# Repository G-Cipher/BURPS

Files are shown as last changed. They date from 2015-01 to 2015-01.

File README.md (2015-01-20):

BURPS
=====

BeagleBone Universal Removed Pololu Steppers

BeagleBone Black cape providing a semi-generic optoisolated breakout for 4
stepper axis outputs and 3 limit switch inputs. The BBB I/O pin configuration
is chosen for compatibility with [BeagleG] for testing purposes.
Output is a male DB-25 connector, with pinout selected for compatibility with
[FlashCut CNC] stepper driver electronics.

BURPS is therefore a stripped-down implementation of [BUMPS], the
BeagleBone Universal Multi Pololu Steppers board.

The BURPS PCB design files were created with [Cadsoft Eagle] 5.12.0. This
board is designed for a prototype milling process, and may not be suitable
for commercial fabrication.

PCB v1.0 uses a male DB-25 connector mounted on the bottom of the board for
external signals. This was found to conflict with peripherals plugged into
the USB type A or micro HDMI ports.

PCB v1.1 replaces the DB-25 connector with a dual-row 26-pin header. The
pinout of the header corresponds to a male DB-25. A ribbon cable assembly
with header IDC and male DB-25 IDC will connect the signals correctly.

The graphics below depict PCB v1.0.

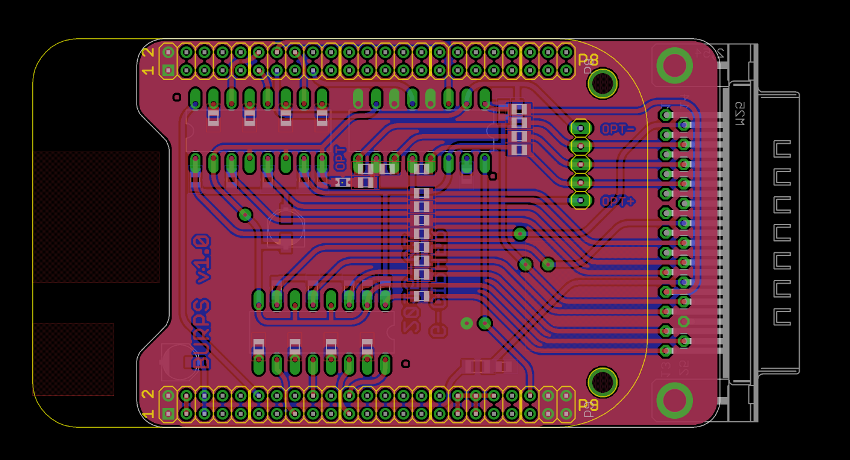
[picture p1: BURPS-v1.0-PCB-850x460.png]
pcb

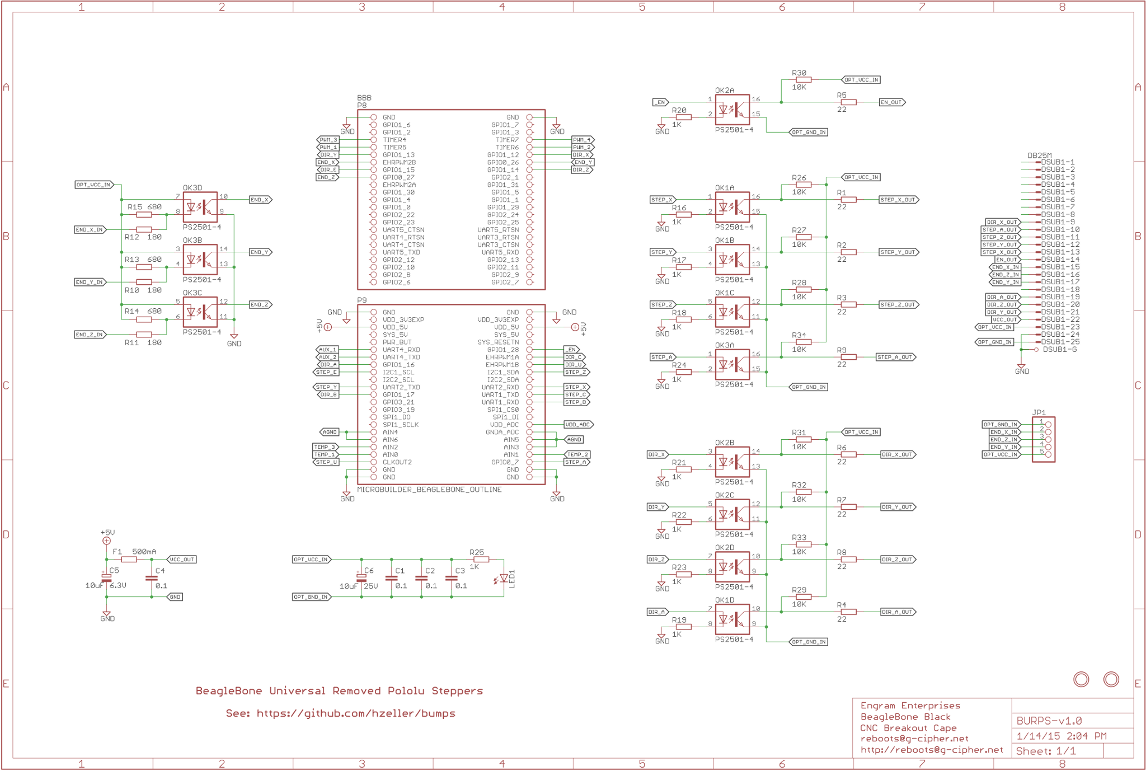
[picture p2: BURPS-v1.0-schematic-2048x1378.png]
schematic


[beagleg]: https://github.com/hzeller/beagleg
[flashcut cnc]: http://www.flashcutcnc.com/cnc-controls/stepper-controls-motors
[bumps]: https://github.com/hzeller/bumps
[cadsoft eagle]: http://www.cadsoftusa.com/
[pcb]: https://raw.githubusercontent.com/G-Cipher/BURPS/master/BURPS-v1.0-PCB-850x460.png
[schematic]: https://raw.githubusercontent.com/G-Cipher/BURPS/master/BURPS-v1.0-schematic-2048x1378.png

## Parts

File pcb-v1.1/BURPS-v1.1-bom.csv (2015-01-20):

Part # | Value | Description | Package | Qty
R1-R9 | 22 ohms | SMT chip resistor | 0805 | 9
R10-R12 | 180 ohms | SMT chip resistor | 0080 | 3
R13-R15 | 680 ohms | SMT chip resistor | 0805 | 3
R16-R25 | 1K | SMT chip resistor | 0805 | 10
R26-R34 | 10K | SMT chip resistor | 0805 | 9
C1-C4 | 0.1uF | SMT chip capacitor | 0805 | 4
C5 | 10uF | Aluminum electrolytic capacitor, 6.5V minimum | Size code C, 5.0mm dia | 1
C6 | 10uF | Aluminum electrolytic capacitor, 25V minimum | Size code C, 5.0mm dia | 1
OK1-OK3 | PS2501-4 | 4-channel optocoupler | DIP-16 | 3
 |  | 16-pin DIP socket (optional) | DIP-16 | 3
LED1 | LH R974 | SMT chip LED (generic) | 0805 | 1
F1 | PTS120615V050 | SMT polyfuse 15V 0.5A or similar | 1206 | 1
JP1 | 1x5 | 2.54mm single row pin header |  | 1
JP2 | 2x13 | 2.54mm dual row pin header |  | 1
P8,P9 | 2x26 | 2.54mm dual row pin header |  | 2

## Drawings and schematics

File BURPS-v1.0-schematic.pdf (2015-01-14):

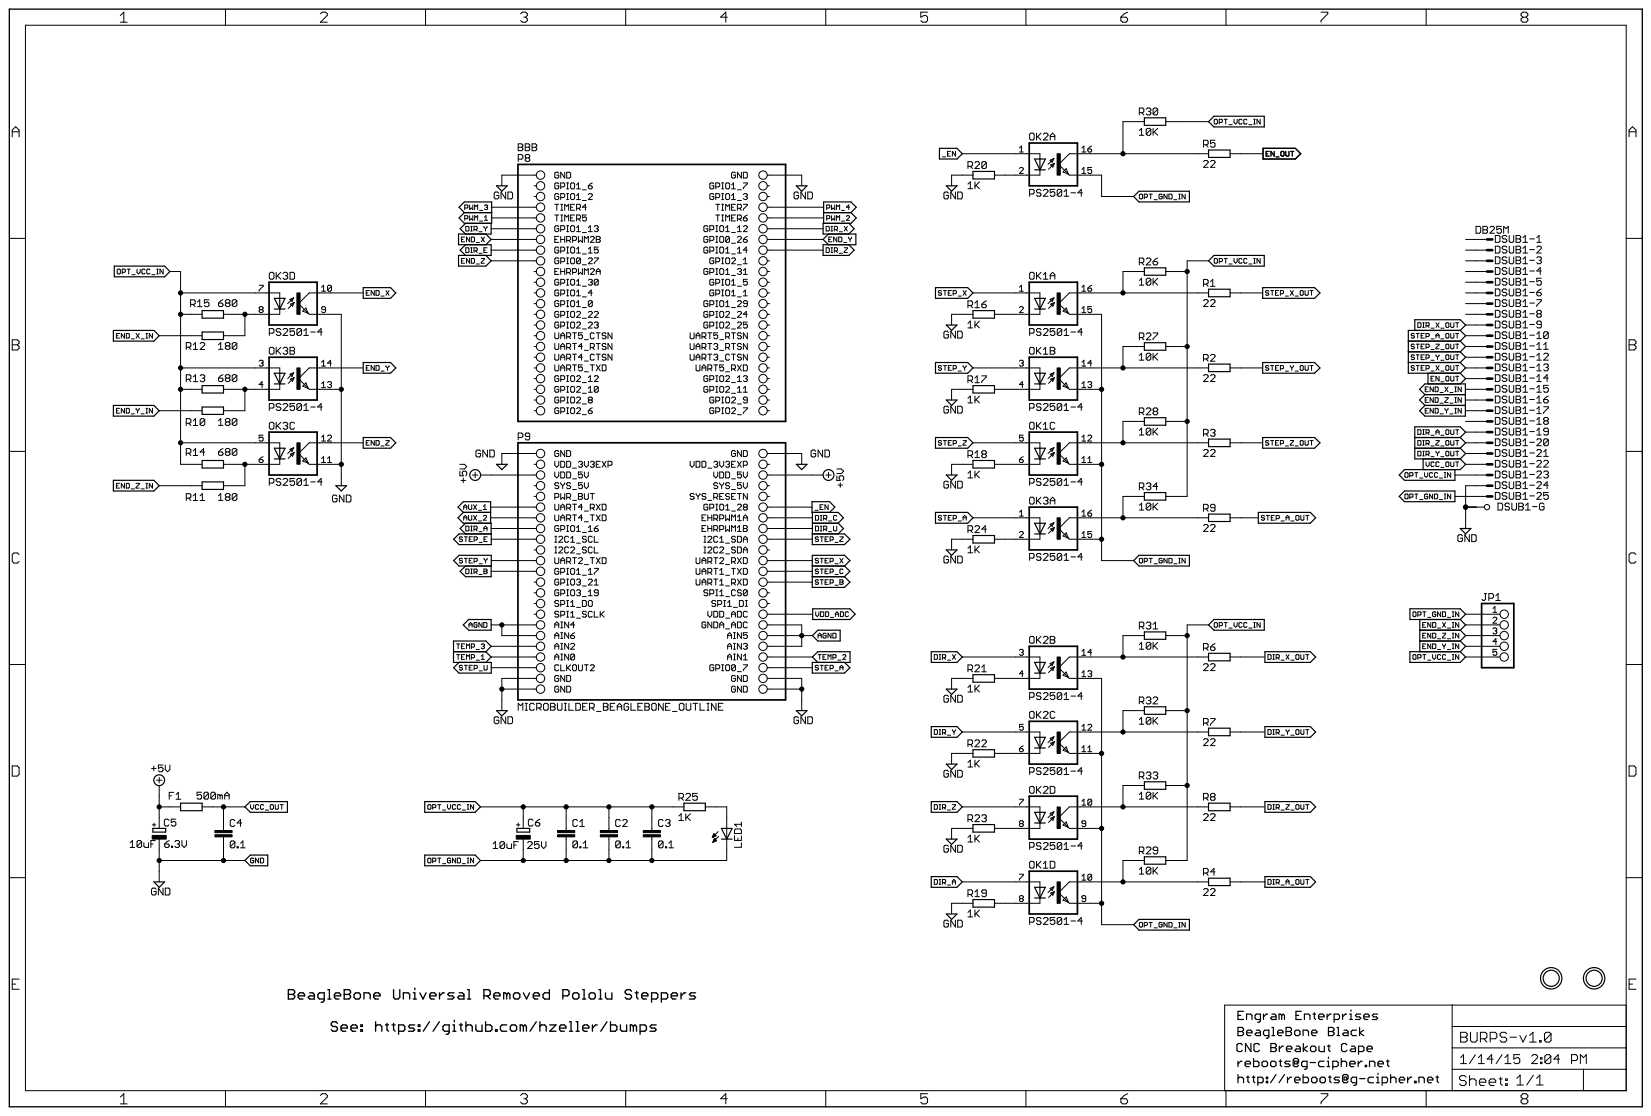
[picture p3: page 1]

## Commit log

2015-01-14 First PCB revision, v1.0
    [BURPS-v1.0.brd, BURPS-v1.0.sch]
2015-01-14 new file: BURPS-v1.0-PCB-850x460.png
2015-01-14 Added new file BURPS-v1.0-schematic-2048x1378.png
2015-01-14 modified: pcb/BURPS-v1.0.brd
    [BURPS-v1.0.brd]
2015-01-20 v1.0 design files moved to pcb-v1.0. v1.1 design files added to pcb-v1.1.
    [BURPS-v1.0.brd, BURPS-v1.0.sch, BURPS-v1.1.brd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]
2015-01-20 modified: README.md to reflect PCB v1.1
2015-01-20 modified: pcb-v1.1/BURPS-v1.1.brd
    [BURPS-v1.1.brd]
2015-01-20 new file: pcb-v1.0/BURPS-v1.0-bom.csv new file: pcb-v1.1/BURPS-v1.1-bom.csv
    [BURPS-v1.0-bom.csv, BURPS-v1.1-bom.csv]
